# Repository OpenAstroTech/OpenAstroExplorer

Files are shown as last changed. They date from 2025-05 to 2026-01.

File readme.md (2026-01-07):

# OpenAstroExplorer

OAE

[3D view](https://a360.co/4jmfOcc)

v1.0 released now! 

The OpenAstroExplorer is a compact and portable equatorial mount designed for light to midrange astrophotography setups.

It features a fully belt driven RA axis, resulting in very low backlash and PE, using the same two-stage 9:1 gearbox as OAM. It also includes a magnetically detachable RA ring, a compact worm gear driven DEC axis, and a foldable ALTAZ mechanism, optimized for easy transportation and quick setup in the field. Despite its focus on portability, the OAE offers precise tracking and guiding with a good payload capacity.

A built-in Auto Polar Alignment (AutoPA) mechanism simplifies setup, making the mount user-friendly for both experienced and new astrophotographers. 

While it doesn’t match the payload capacity of the [OpenAstroMount](https://github.com/OpenAstroTech/OpenAstroMount), the OAE excels in convenience and versatility, perfect for grab-and-go sessions or travel setups. (It also doesn't weigh 12kg)

Specs
| Weight | Cost | Payload | Performance (PHD2)
|--|--|--|--
| 3kg + Tripod <br>& counterweights | 200-350$ | 5kg | 0.6-0.9" RMS

---
### Links

[BOM](https://docs.google.com/spreadsheets/d/1VRqLXc0toShZgP3rCiKZRFy2YImOhnwUEP0JS75wGOw/edit?usp=sharing)

[Printed Parts](https://docs.google.com/spreadsheets/d/12bo7vfit7GZXNui0Y1q4IBbTn9S2-HQub6Z6bK9Nim4/edit?usp=sharing)

[Guides](https://wiki.openastrotech.com/en/OpenAstroExplorer)

---
[Join our Discord!](https://discord.gg/5GVtSN59GB)
---

<br /> <a href="https://github.com/OpenAstroTech/OpenAstroExplorer"> OpenAstroExplorer </a> &copy; 2026 by <a href="https://github.com/OpenAstroTech">OpenAstroTech </a> is licenced under <a rel="license" href="http://creativecommons.org/licenses/by-nc/4.0/">CC BY-NC 4.0</a>.

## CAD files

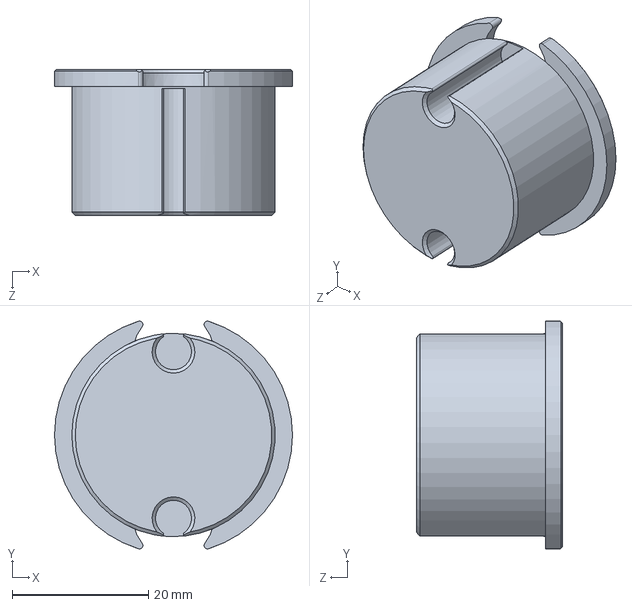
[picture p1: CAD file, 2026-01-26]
CAD/Solidworks/ALTAZ/AZ_coupler.SLDPRT
35.0 x 33.5 x 21.5 mm

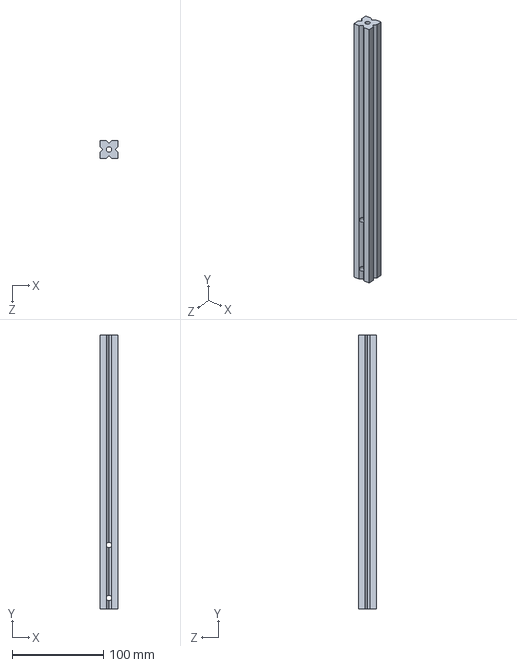
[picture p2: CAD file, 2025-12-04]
CAD/Solidworks/assembly/2020 300.SLDPRT
20.0 x 300.0 x 20.0 mm

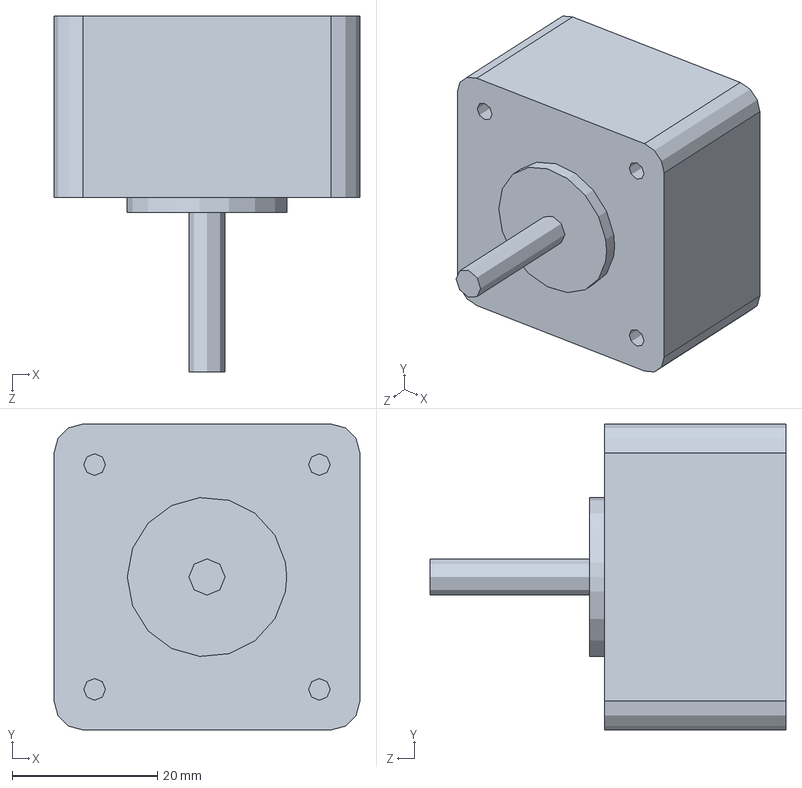
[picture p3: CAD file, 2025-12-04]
CAD/Solidworks/assembly/Electronics/NEMA 17 lang.SLDPRT
42.2 x 42.2 x 49.1 mm

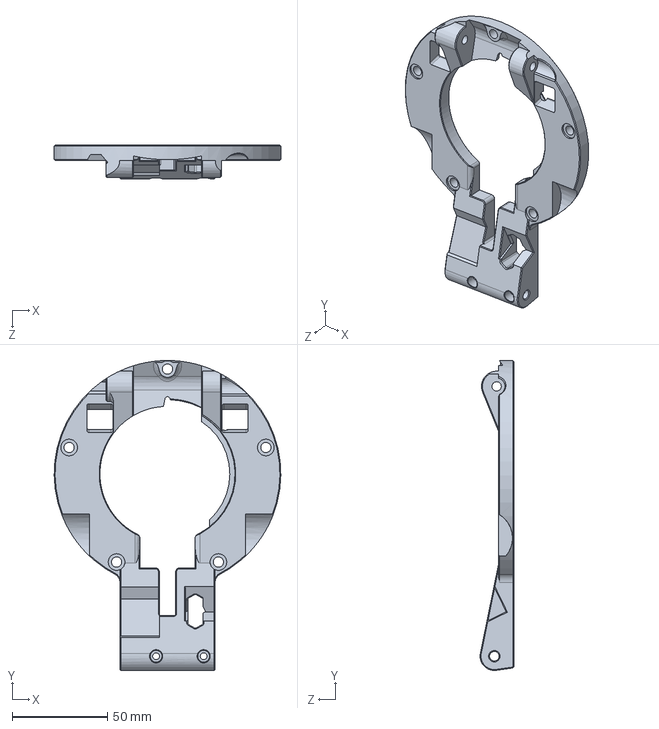
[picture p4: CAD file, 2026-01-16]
CAD/Solidworks/Base/bottom_v2.SLDPRT
119.2 x 163.0 x 17.8 mm

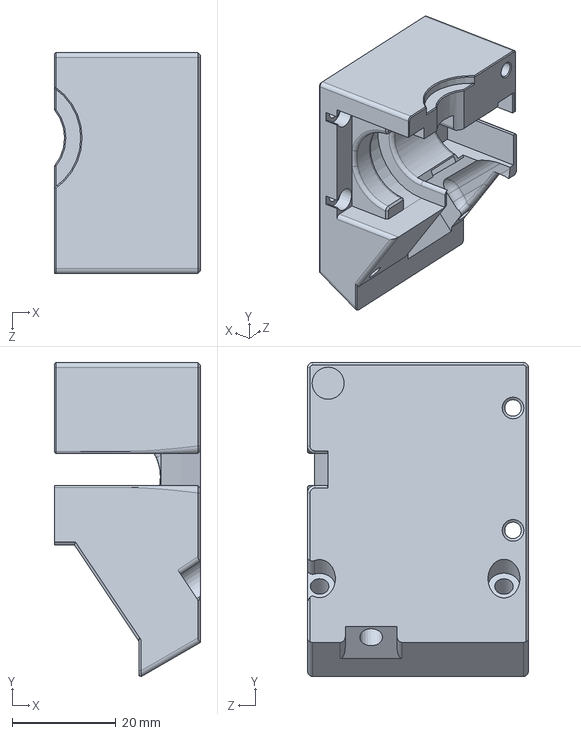
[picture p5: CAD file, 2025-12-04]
CAD/Solidworks/DEC/DEC_gearbox.SLDPRT
28.2 x 60.6 x 42.7 mm

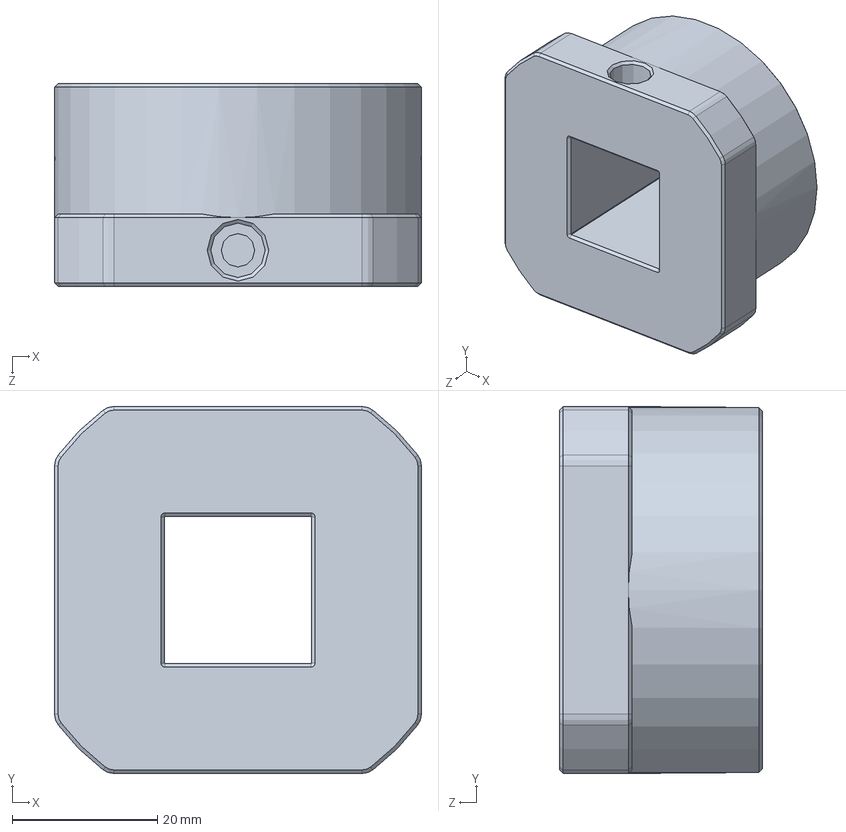
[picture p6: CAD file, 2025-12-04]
CAD/Solidworks/other/CW_attachment_2inch.SLDPRT
50.6 x 50.6 x 28.0 mm

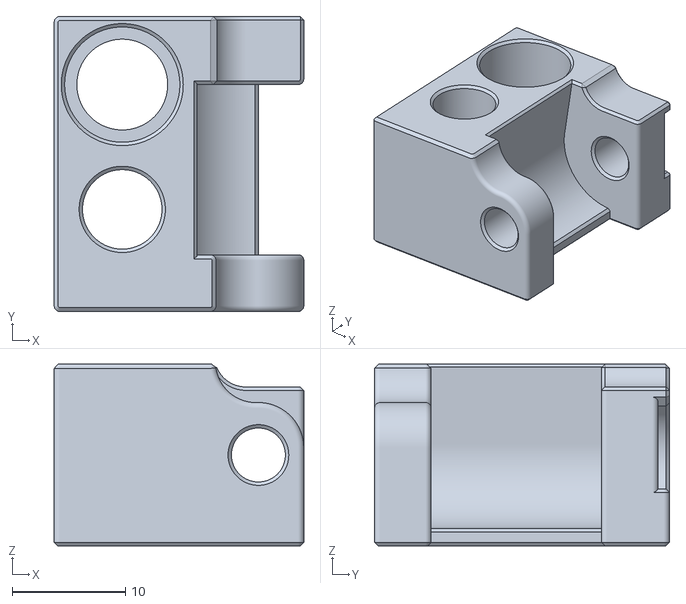
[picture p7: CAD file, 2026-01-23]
STL/ALTAZ/AZ_slider.STL
22.0 x 26.0 x 16.0

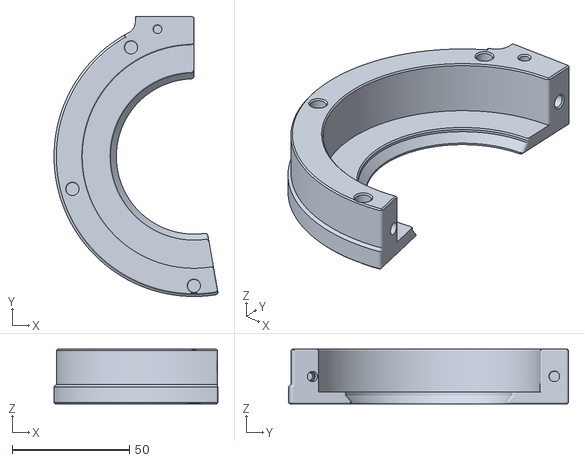
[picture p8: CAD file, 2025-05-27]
STL/base/6012_base_left_top.STL
69.8 x 119.2 x 23.3

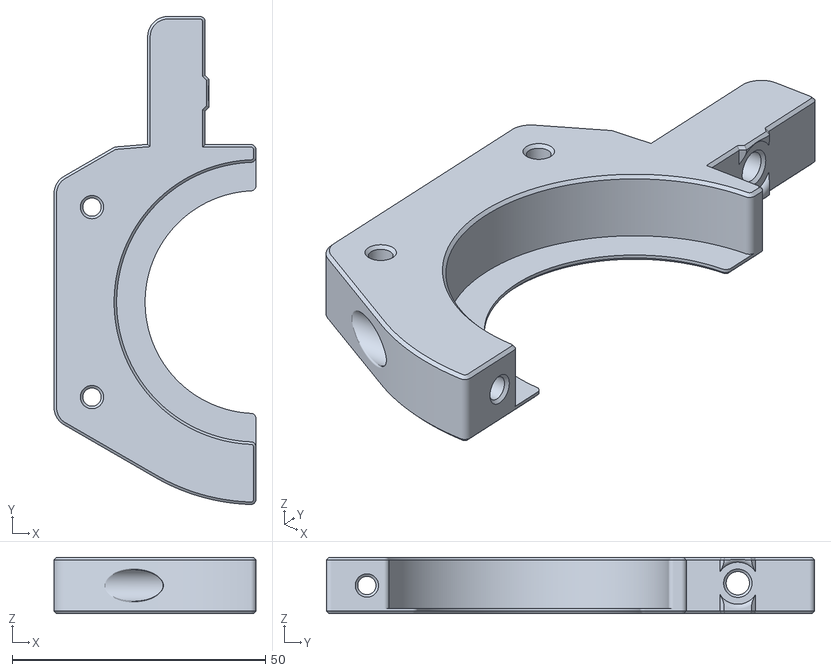
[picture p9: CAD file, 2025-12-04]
STL/DEC/DEC_holder_rear_left.STL
39.9 x 96.4 x 11.1

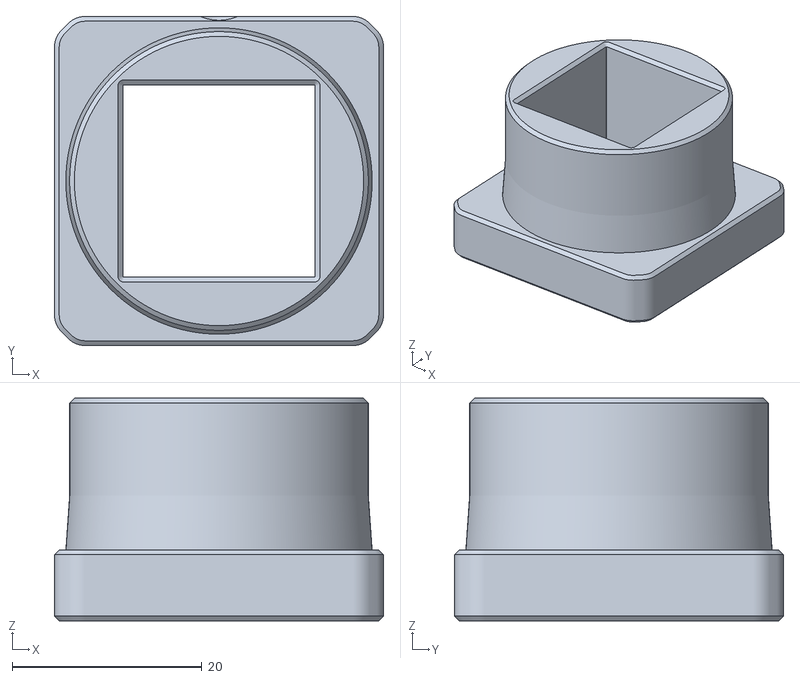
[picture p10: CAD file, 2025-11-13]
STL/other/CW_attachments/CW_attachment_32mm.STL
34.7 x 34.7 x 23.5

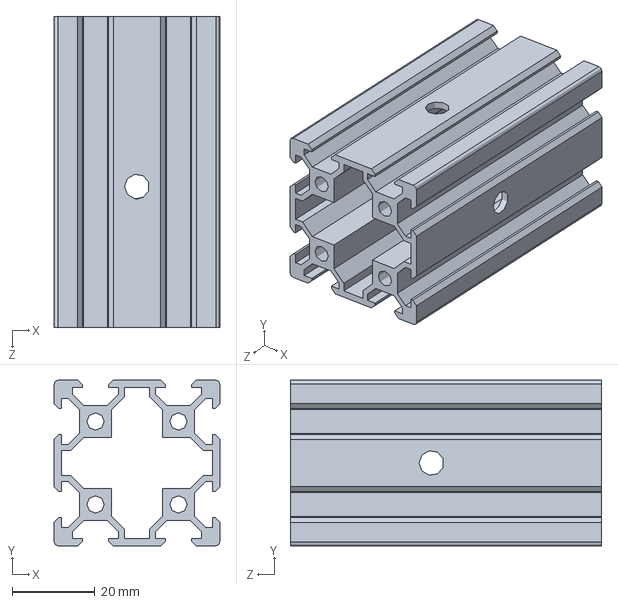
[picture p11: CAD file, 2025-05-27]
CAD/Solidworks/assembly/4040_dual_slot.SLDPRT
40.0 x 40.0 x 75.0 mm

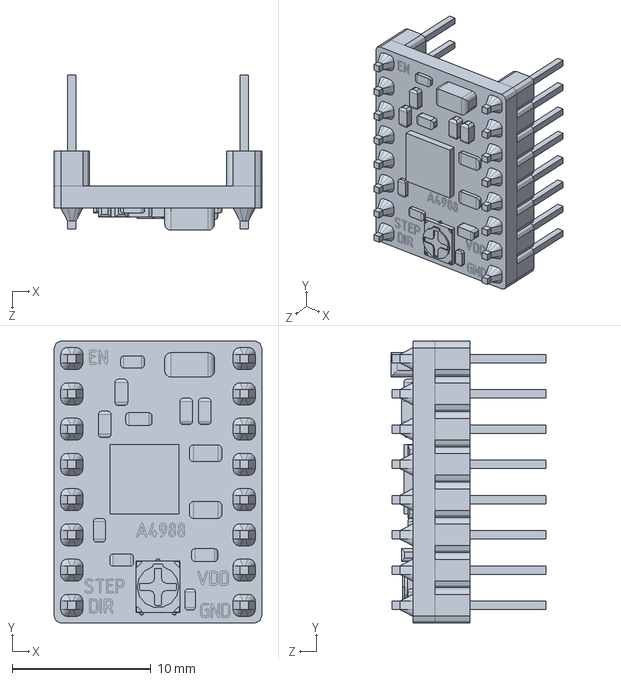
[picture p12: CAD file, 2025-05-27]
CAD/Solidworks/assembly/Electronics/a4988-stepper-driver-withpins.SLDPRT
15.0 x 20.3 x 11.2 mm

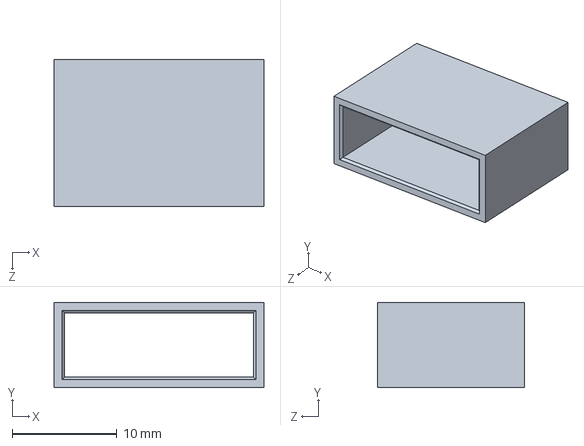
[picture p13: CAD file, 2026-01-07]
CAD/Solidworks/Base/belt_holder_clip.SLDPRT
20.0 x 8.10 x 14.0 mm

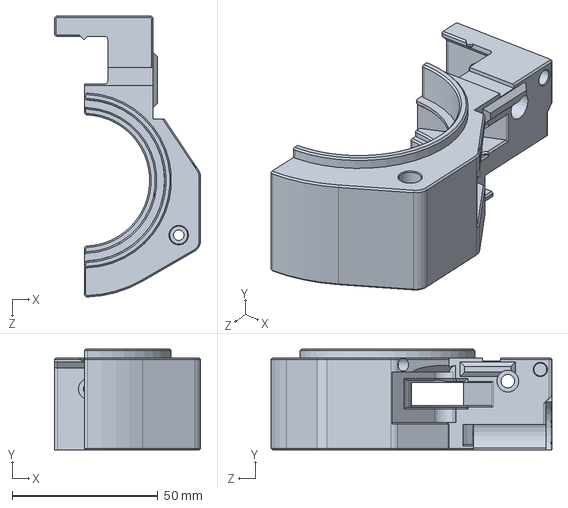
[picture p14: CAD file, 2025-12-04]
CAD/Solidworks/DEC/DEC_holder_front_right_v2.SLDPRT
50.1 x 34.6 x 96.4 mm

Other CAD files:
CAD/Solidworks/OpenAstroExplorer_v1.0.1.SLDASM
CAD/Solidworks/RA_gearbox/Tensioner_slide.SLDASM
CAD/Solidworks/ALTAZ/AZ_slider_v2.SLDPRT
CAD/Solidworks/other/CW_attachment_retainer.SLDPRT
CAD/Solidworks/ALTAZ/51111_adapter_left.SLDPRT
CAD/Solidworks/ALTAZ/51111_adapter_right.SLDPRT
CAD/Solidworks/ALTAZ/51111_adapter_v2.SLDPRT
CAD/Solidworks/ALTAZ/ALT_Knob.SLDPRT
CAD/Solidworks/ALTAZ/ALT_slider.SLDPRT
CAD/Solidworks/ALTAZ/AZ_connector.SLDPRT
CAD/Solidworks/ALTAZ/ESP_lid.SLDPRT
CAD/Solidworks/ALTAZ/MGN9C_adapter.SLDPRT
CAD/Solidworks/ALTAZ/driver_lid.SLDPRT
CAD/Solidworks/Base/4040adapter_front.SLDPRT
CAD/Solidworks/Base/4040adapter_mid.SLDPRT
CAD/Solidworks/Base/4040adapter_rear.SLDPRT
CAD/Solidworks/Base/6012_base_v2.SLDPRT
CAD/Solidworks/Base/CW_Knob.SLDPRT
CAD/Solidworks/Base/Handle.SLDPRT
CAD/Solidworks/Base/RA Ring.SLDPRT
CAD/Solidworks/Base/RA_ring_inner.SLDPRT
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

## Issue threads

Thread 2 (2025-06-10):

Difference between the BOM and the STEP file

carozoynarizota, 2025-06-10:
Hi! The BOM says that two flat screews will be needed in case of EQ5 mount:

M5 x 20 Flathead |   | 2 |   | used only for EQ5 Tripod adapter

But from the STEP file (OpenAstroExplorer_v1.0.STEP) I can only see two M5x25mm flat sreews that I suppose are the ones intended in the BOM.

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

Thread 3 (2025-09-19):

Request to add BOM and place-and-pick for board

bretbenz84, 2025-09-19:
Thanks for providing the Gerber files and project files. I tried to order a pre-made board from you but it won't let me ship to California. If I were to upload it to jlcpcb.com I would need a BOM and pick-and-place. Can you export those from the Altium project and upload them into the PCB folder? I don't have access to Altium.

Elenedeath, 2025-09-20:
you can open the file [ProPrj_OAE board.epro](https://github.com/OpenAstroTech/OpenAstroExplorer/blob/master/PCB/ProPrj_OAE%20board.epro) with [EasyEDA](https://easyeda.com/) like that you can export both gerber, BOM and pick-place.

CAUTION to use easyEDA pro not the standard one.

you can also directly export the project when do "File > export > Gerber " instead of click "export gerber" click "order pcb"

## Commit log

2023-08-18 v0.1 initial release
    [2020 200.SLDPRT, 4040_dual_slot.SLDPRT, 4040adapter_front.SLDPRT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]
2024-03-03 OAE v0.2
    - added DEC axis
    - slight rework to RA Ring parts
    [2020 200.SLDPRT, 2020 300.SLDPRT, 2020 50.SLDPRT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]
2024-03-18 fix DEC covers
    [cover_left.STL, cover_right.STL]
2025-05-22 add PCB files
2025-05-27 v1.0 release
    [2020 200.SLDPRT, 2020 300.SLDPRT, 2020 50.SLDPRT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]
2025-06-02 parts updates
    minor adjustments, no reprint required
    [ALT_slider.SLDPRT, DEC_gearbox.SLDPRT, RA_ring_inner.SLDPRT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]
2025-06-02 update MGN9C_adapter
    made home indicator smaller so it doesn't collide anymore
    [MGN9C_adapter.SLDPRT]
2025-06-05 add Counterweight adapters
    [CW_attachment_2inch.SLDPRT, CW_attachment_2inch.STL, CW_attachment_31.5mm.SLDPRT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]
2025-06-13 update 51111_adapter
    - Changed the part so the single M5 flat nut is no longer required
    - added all the split parts to the STEP export
    [51111_adapter_left.SLDPRT, 51111_adapter_right.SLDPRT, 51111_adapter_v2.SLDPRT]
2025-11-10 add spacer for EQ5 Tripods
    [EQ5_spacer.SLDPRT, EQ5_spacer.STL]
2025-11-12 parts for aluminum EQ5 Tripods
    [Tripod_adapter_EQ5_alu.SLDPRT, Tripod_adapter_EQ5_alu_left.SLDPRT, Tripod_adapter_EQ5_alu_left.STL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]
2025-11-13 update counterweight attachments
    [CW_attachment_28mm.SLDPRT, CW_attachment_28mm.STL, CW_attachment_2inch.SLDPRT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]
2025-12-04 update OAE 1.0.1
    - made DEC slightly sturdier
    - added support for 12mm dia worm gears
    Changes parts: all 4 DEC holder parts, both wormshaft holders, DEC gearbox, both outer RA Rings
    [2020 300.SLDPRT, CW_Knob.SLDPRT, CW_attachment_28mm.SLDPRT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]
2026-01-07 Update belt holder
    - Improved design of the belt holder so it can not slip
    [belt_holder.SLDPRT, belt_holder.STL, belt_holder_clip.SLDPRT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]
2026-01-08 update AZ_coupler
    - improve design for sturdyness. Requires 2 M5x25 and 2 Shims or Washers instead of M5x20FH
    [AZ_coupler.SLDPRT, AZ_coupler.STL]
2026-01-16 minor tolerance changes
    - fix an issue on 51111_adapter where AZ mechanism could interfere
    - minor adjustment of screw locations of AZ_coupler
    - removed hex holes from bottom_v2
    [51111_adapter_left.SLDPRT, 51111_adapter_left.STL, 51111_adapter_right.SLDPRT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]
2026-01-23 minor tolerance adjustments
    [4040adapter_mid.STL, AZ_slider.STL, AZ_slider_v2.SLDPRT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]
2026-01-26 minor adjustment
    - Make AZ_coupler compatible with M5 flathead screw with flange (ISO 7380-2)
    [AZ_coupler.SLDPRT, AZ_coupler.STL]
